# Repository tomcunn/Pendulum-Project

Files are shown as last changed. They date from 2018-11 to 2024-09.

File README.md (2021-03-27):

# Pendulum-Project
Inverted Pendulum code runs a stepper motor to control the position of a cart equipped with a pendulum. 

# Issues
* One of the key things to overcome was how to implement the encoder. One of the problems was drift of the encoder when I tried to implement the code myself. I ended up using an encoder library which solved the issue because they were using X4 encoding. This means that the position is updated on every edge of both channels. The overall accuracy of the cheap encoders is pretty incredible. 

* Another issue is the speed of the stepper, overall steppers are pretty slow and acceleration limited. Translating the code from timing pulses, to steps, to inches, to speeds is a little cumbersome in the code. Overall the cheap stepper drivers have worked just fine.

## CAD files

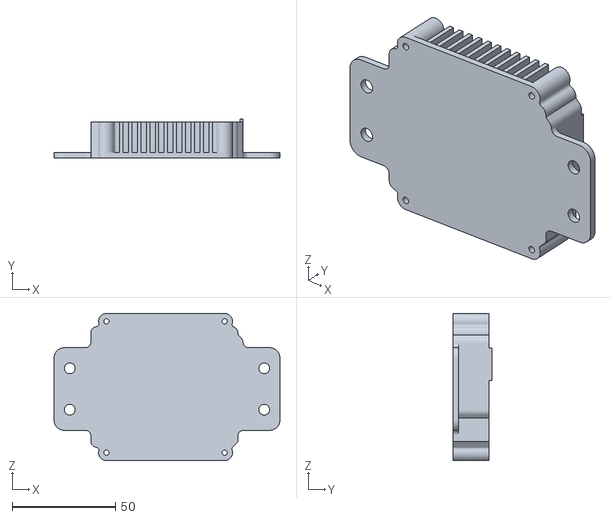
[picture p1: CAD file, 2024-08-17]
MechanicalDesignFiles/stl/Pendulum_Arduino_Case.stl
109.2 x 18.7 x 71.1

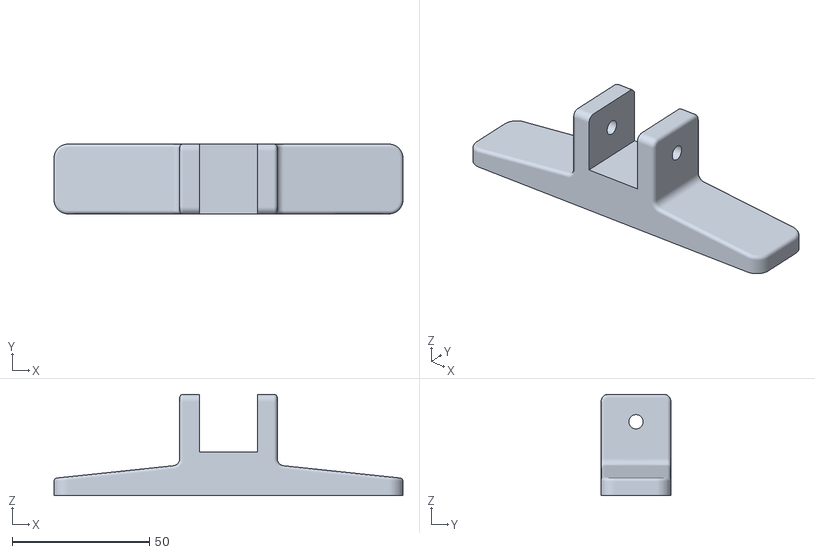
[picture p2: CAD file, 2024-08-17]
MechanicalDesignFiles/stl/Foot.stl
127.0 x 25.4 x 36.9

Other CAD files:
MechanicalDesignFiles/fusion_files/ArduinoUnoCasePendulum.f3d

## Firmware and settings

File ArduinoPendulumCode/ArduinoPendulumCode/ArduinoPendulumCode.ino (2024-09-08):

//**************************************
//*   Open Pendulum Control Platform Interface
//*   8/25/2024
//*   Cunningham
//***************************************

#include <avr/io.h>
#include <avr/interrupt.h>
#define ENCODER_OPTIMIZE_INTERRUPTS
#include <Encoder.h>


//Hardware Assignments
#define  LIMIT_HOME   A3
#define LED_GREEN  10  
#define LED_YELLOW 9
#define LED_RED 8
#define  DIR 11
#define  STEP 12
#define  SWITCH1 4
#define  SWITCH2 A2
#define  EncoderChannel_A  2
#define  EncoderChannel_B  3

#define  MAX_CART_VELOCITY  500  //875
#define  MAX_CART_ACCELERATION  50 //100

//Function prototypes
void  SetupTimer1(void);
void  SetupTimer0(void);

//Global Variables
uint8_t RunTask_10ms = 0;


volatile unsigned int StepSpeed = 0;

//Create and instance of the encoder module
Encoder PendulumPosition(EncoderChannel_A, EncoderChannel_B);

  //Create a structure for movement data
struct MovementParms
{
  signed int Count;
  signed int Position;
  signed int Velocity;
  signed int Acceleration;
  signed int Direction;
};

struct PendulumData
{
  //Create instance of three structures 
  volatile struct MovementParms DesiredCart;
  volatile struct MovementParms CurrentCart;
  volatile struct MovementParms EncoderValue;
};

PendulumData pd;

//**************************************
//  Interrupt used to generate the servo 
//  pulses
//  The lower the address the higher is the priority level
//  Vector Address 12 
//**************************************
ISR(TIMER1_COMPA_vect)  
{   
   if(StepSpeed < 64000)
   {
     //Check the direction pin and determine the position
     if(pd.CurrentCart.Direction == 1)
     {
        digitalWrite(DIR,1);
        pd.CurrentCart.Count++;
     }
     else
     {
       digitalWrite(DIR,0);
       pd.CurrentCart.Count--;
     }
  
     //Step once
     digitalWrite(STEP,1);
     digitalWrite(STEP,0);
   }
   //Interrupt occurs when timer matches this value
   //Larger velocity means smaller OCR1A value
   //StepSpeed is calculated using another function and then stored 
   //in a global variable to be accessed by the interrupt routine
   OCR1A = StepSpeed;
}

//**************************************
//  10 ms Task Rate
//  Creates a periodic Task 
//  Vector Address 15
//**************************************
ISR(TIMER0_COMPA_vect)
{
  RunTask_10ms = 1;
}

//*******************************************
// WriteStepSize
//
// Pass in a velocity and update the step size
// global variable which is read by the interrupt
// to generate the stepper pulses. Speed is in 
// the units mm/sec. 
//*******************************************
void WriteStepSize(signed int Speed)
{
  //Set the direction pin based on the sign of the speed
  if(Speed > 0)
  {
     pd.CurrentCart.Direction = 1;
  }
  else
  {
     pd.CurrentCart.Direction = 0;
  } 
  
  //Check to prevent overflows, StepSpeed is 16 bit
  if(Speed > 2 || Speed < -2)
  {
     //This is derived from the table above using a Power trendline
     StepSpeed = (signed int)(591733/(abs(Speed)));
  }
  //This is like setting it to zero speed
  else
  {
     StepSpeed = 65000;
  }
}

//***********************************
//  MotionAccelerationControl
//
//
//***********************************
void MotionAccelerationControl(void)
{
   //Acceleration is a signed value
   //If positive check to make sure it is not bigger than max V
   //else check the - max speed
   
   if(pd.DesiredCart.Acceleration >= 0)
   {
      if(pd.CurrentCart.Velocity < (MAX_CART_VELOCITY + pd.DesiredCart.Acceleration))
      {
         pd.CurrentCart.Velocity += pd.DesiredCart.Acceleration; 
      }
      else
      {
        pd.CurrentCart.Velocity = MAX_CART_VELOCITY;
      }
   }
   else
   {
      if(pd.CurrentCart.Velocity > (-MAX_CART_VELOCITY + pd.DesiredCart.Acceleration))
      {
         pd.CurrentCart.Velocity += pd.DesiredCart.Acceleration;
      }
      else
      {
         pd.CurrentCart.Velocity = -MAX_CART_VELOCITY;
      }
   }

   WriteStepSize(pd.CurrentCart.Velocity);
}
//*********************************************
//  SetupTimer0
//
//  Used to generate the 10 ms task rate
//*********************************************
void SetupTimer0()
{
  TCCR0A = 0; // set entire TCCR0A register to 0
  TCCR0B = 0; // same for TCCR0B
  TCNT0  = 0; //initialize counter value to 0
  // set compare match register for 2khz increments
  OCR0A = 155;// = (16*10^6) / (100*1024) - 1 = 155(must be <256)
  // turn on CTC mode
  TCCR0A |= (1 << WGM01);
  // 1024 prescaler - page 142 of datasheet
  TCCR0B |= (1 << CS00); 
  TCCR0B |= (1 << CS02);  
  // enable timer compare interrupt
  TIMSK0 |= (1 << OCIE0A);
}

//*********************************************
// SetupTimer1
//
//  Used to generate the stepper motor pulses
//********************************************
void SetupTimer1()
{
  //TCCRnA/B- Stands for Timer/Counter Control Registers.
  TCCR1A = 0;
  TCCR1B = 0;

  //TCNTn- Stands for Timer/Counter Register.
  TCNT1 = 0; // initialize the counter from 0

  //OCRnA/B- Stands for Output Compare Register.
  OCR1A = 65000; // sets the counter compare value

  //TIMSKn- Stands for Timer/Counter Mask In Registers.
  TCCR1B |= (1<<WGM12); // enable the CTC mode
  TCCR1B |= (1<<CS11); // 1/8 Prescale, 0 prescale was not working

  TIMSK1 |= (1<<OCIE1A); 
}



//****************************************
//  Setup
//
//****************************************
void setup()
{
  //Initialize Variables
  pd.CurrentCart.Velocity = 0;
  pd.DesiredCart.Velocity = 0;
  pd.CurrentCart.Count = 0;
  pd.DesiredCart.Acceleration = 1;

  //Setup Inputs
  pinMode(LIMIT_HOME, INPUT);
  pinMode(SWITCH1, INPUT);
  pinMode(SWITCH2, INPUT);
  pinMode(EncoderChannel_A, INPUT);
  pinMode(EncoderChannel_B, INPUT);

  //Setup Outputs
  pinMode(LED_GREEN,OUTPUT);
  pinMode(LED_YELLOW,OUTPUT);
  pinMode(LED_RED,OUTPUT);
  pinMode(STEP,OUTPUT);
  pinMode(DIR,OUTPUT);

  //Disable interrupts
  cli();
  
  //Setup Timers
  SetupTimer0();

  SetupTimer1();
  
  //enable interrupts
  sei();
  Serial.begin(115200);
}

//*********************************************
// Return Home
//
//********************************************
bool ReturnHome()
{
   bool home = false;

   digitalWrite(LED_RED,HIGH);
   digitalWrite(LED_GREEN,HIGH);
   
   if(pd.CurrentCart.Position > 5)
   {
      pd.DesiredCart.Velocity = -100;
   }
   else if(pd.CurrentCart.Position < -5)
   {
     pd.DesiredCart.Velocity = 100;
   }
   
   //Determine which direction to go
   if(!digitalRead(LIMIT_HOME))
   {
      pd.CurrentCart.Count = 0;
      pd.DesiredCart.Velocity = 0;
      pd.CurrentCart.Velocity = 0;
      pd.DesiredCart.Acceleration = 0;
      home = true;
   }
   WriteStepSize(pd.DesiredCart.Velocity);
   return home;
}

void PID_Loop()
{
  int error = 0;
  static int pre_error = 0;

  error = pd.EncoderValue.Count;

  //Try
  // P = 0.75
  // D = 2.0

  // P = 0.6
  // D = 4.0  Better

  // P = 0.6
  // D = 8.0 
  pd.DesiredCart.Acceleration = (int)((float)error * 0.6f) + ((float)(error - pre_error) * 8.0f) ;
  pre_error = error;  
}

void SendSerialData()
{
   // Send the three structures as binary data
   Serial.write((byte*)&pd,  sizeof(pd));
}

void loop()
{
  static int counter;
  static int previous_position;
  static bool homed = false;
  static bool homing = false;
  static bool start_control = false;

  if(RunTask_10ms)
  {
    counter++;
    if(counter > 2)
    {
      //SendSerialData();
      counter = 0;
    }
    //The Encoder has 2400 pulses per rev
    pd.EncoderValue.Count = -1*PendulumPosition.read();
    pd.EncoderValue.Position = (signed int)((float)pd.EncoderValue.Count/6.66666);
    
    //Turn the number of counts in a position in mm
    pd.CurrentCart.Position = (signed int)((float)pd.CurrentCart.Count/3.3799);

    //Serial.println(pd.EncoderValue.Position);

    digitalWrite(LED_YELLOW,HIGH);
    
    if(digitalRead(SWITCH2))
    {
      start_control = true;
      digitalWrite(LED_GREEN,HIGH);
    }
    else if(digitalRead(SWITCH1))
    {
      start_control = false;
      digitalWrite(LED_RED,HIGH);
    }


    //If both Switches are pressed return home
    if(digitalRead(SWITCH2) && digitalRead(SWITCH1))
    {
      homing = true;
      start_control = false;
    }

    //Exit the homing logic.    
    if(homed == true)
    {
      homing = false;
      homed = false;
    }

    //Return back home using this function
    if((homing==true) && (homed == false))
    {
      start_control = false;
      homed = ReturnHome();
    }
    else
    {
       if(start_control == true)
       {
        PID_Loop();
        MotionAccelerationControl();
       }
       else
       {
        pd.CurrentCart.Velocity = 0;
        WriteStepSize(pd.CurrentCart.Velocity);
       }
    }

    if(pd.EncoderValue.Position > 10 || pd.EncoderValue.Position < -10)
    {
      start_control = false;
    }

    Serial.print(homing);
    Serial.print(",");
    Serial.print(homed);
    Serial.print(",");
    Serial.println(pd.CurrentCart.Position);


    pd.EncoderValue.Acceleration = TCNT0;
    pd.EncoderValue.Velocity = 75;
    pd.EncoderValue.Direction = 30000;
    RunTask_10ms = 0;
  }
}

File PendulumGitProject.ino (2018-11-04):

//**************************************
//*   AI Pendulum Control Platform Interface
//*   4/6/2018
//*   Cunningham
//***************************************

#include <avr/io.h>
#include <avr/interrupt.h>
#define ENCODER_OPTIMIZE_INTERRUPTS
#include <Encoder.h>

//Hardware Assignments
#define  EncoderChannel_A  2
#define  EncoderChannel_B  3
#define  Step 12
#define  Dir  11
#define  MAX_CART_VELOCITY  30000
#define  MAX_CART_ACCELERATION  2000

#define LED_GREEN  10  
#define LED_YELLOW 9
#define LED_RED 8

#define  PGAIN 750

//Function prototypes
void  SetupTimer1(void);
void  SetupTimer0(void);
void  Encoder_ISR(void);
void  WriteStepSize(int Speed);
void  MotionVelocityControl(void);
void  MotionAccelerationControl(void);

//Create a structure for movement data
struct MovementParms
{
  signed int Position;
  signed int Velocity;
  signed int Acceleration;
  bool Direction;
};

//Create instance of three structures 
volatile struct MovementParms DesiredCart;
volatile struct MovementParms CurrentCart;
volatile struct MovementParms EncoderValue;

//Static Variables that are accessed in interrupts
volatile unsigned int abs_Current_Velocity = 0;
volatile unsigned int Counter = 0;
volatile unsigned int StepSpeed = 0;
volatile signed long timestep = 0;
volatile bool RunTask_10ms = 0;
byte SerialControlData1 = 0;
byte SerialControlData2 = 0;
bool SerialControlDirection = 0;
static bool ReturnHomeFlag = 0;
static unsigned int EncoderStableCount = 0;

byte serial_buffer[5] = {0,0,0,0,0};
int ByteCount;
static int integrator = 0;
Encoder PendulumPosition(EncoderChannel_A, EncoderChannel_B);

//**************************************
//  Interrupt used to generate the servo 
//  pulses
//  The lower the address the higher is the priority level
//  Vector Address 12 
//**************************************
ISR(TIMER1_COMPA_vect)  
{   
   if(StepSpeed < 64000)
   {
     //Check the direction pin and determine the position
     if(CurrentCart.Direction == 1)
     {
        digitalWrite(Dir,1);
        CurrentCart.Position++;
     }
     else
     {
       digitalWrite(Dir,0);
       CurrentCart.Position--;
     }
  
     //Step once
     digitalWrite(Step,1);
     digitalWrite(Step,0);
   }
   //Interrupt occurs when timer matches this value
   //Larger velocity means smaller OCR1A value
   //StepSpeed is calculated using another function and then stored 
   //in a global variable to be accessed by the interrupt routine
   OCR1A = StepSpeed;
}

//**************************************
//  10 ms Task Rate
//  Creates a periodic Task 
//  Vector Address 15
//**************************************
ISR(TIMER0_COMPA_vect)
{
  //Check to see if the flag was not cleared, this will track 
  //overruns in the 10ms task
  if(RunTask_10ms)
  {
    digitalWrite(LED_BUILTIN,1);
  }
  RunTask_10ms = 1;
}

//*******************************************
// WriteStepSize
//
// Pass in a velocity and update the step size
// global variable which is read by the interrupt
// to generate the stepper pulses. Speed is in 
// the units mm/min. 
//*******************************************
void WriteStepSize(signed int Speed)
{
  //Set the direction pin based on the sign of the speed
  if(Speed > 0)
  {
     CurrentCart.Direction = 1;
  }
  else
  {
     CurrentCart.Direction = 0;
  } 
  // Conversion Factor
  //  20000 mm      1 min      360 deg     1 rev       step          4,444 step
  // ----------- x -------- x -------- x -------- x ------------ =  ---------
  //     min        60 sec      rev        120 mm     0.225 deg       sec
  //
  //   16,000,000 cycles      1 sec            3,600 cycles
  //   ----------------- x --------------- = -----------
  //       1 sec             4,444 step          
  //  16,000,000/4,444    = 3,600 clock cycles  (20000 mm/min)
  //  16,000,000/2,222    = 7,200 clock cycles  (10000 mm/min)
  //  16,000,000/666      = 24,024 clock cycles  (3000 mm/min)
  
  //For some reason the prescale set to zero causes problems, so 8 is the minimum
  //which means the clock is 16,000,000/8=2,000,000
  //  2,000,000/4,444   = 450 clock cycles  (20000 mm/min)
  //  2,000,000/2,222    = 900 clock cycles  (10000 mm/min)
  //  2,000,000/666      = 3003 clock cycles (3000 mm/min)

  //To compute position it is 
  // Conversion Factor
  //    360 deg     1 rev       step          13.33 steps
  //  -------- x -------- x ------------ =  ---------
  //     rev        120 mm     0.225 deg        mm

  
  
  //Check to prevent overflows, StepSpeed is 16 bit
  if(Speed > 700 || Speed < -700)
  {
     //This is derived from the table above using a Power trendline
     StepSpeed = (signed int)(9048739L/(abs(Speed)));
  }
  //This is like setting it to zero speed
  else
  {
     StepSpeed = 65000;
  }
}
//*******************************************
//  Configure Timer 1
//*******************************************

void SetupTimer1()
{
  //TCCRnA/B- Stands for Timer/Counter Control Registers.
  TCCR1A = 0;
  TCCR1B = 0;

  //TCNTn- Stands for Timer/Counter Register.
  TCNT1 = 0; // initialize the counter from 0

  //OCRnA/B- Stands for Output Compare Register.
  OCR1A = 65000; // sets the counter compare value

  //TIMSKn- Stands for Timer/Counter Mask In Registers.
  TCCR1B |= (1<<WGM12); // enable the CTC mode
  TCCR1B |= (1<<CS11); // 1/8 Prescale, 0 prescale was not working

  TIMSK1 |= (1<<OCIE1A); 
}

//*********************************************
//  Configure Timer 0
//*********************************************
void SetupTimer0()
{
  TCCR0A = 0; // set entire TCCR0A register to 0
  TCCR0B = 0; // same for TCCR0B
  TCNT0  = 0; //initialize counter value to 0
  // set compare match register for 2khz increments
  OCR0A = 155;// = (16*10^6) / (100*1024) - 1 = 155(must be <256)
  // turn on CTC mode
  TCCR0A |= (1 << WGM01);
  // 1024 prescaler - page 142 of datasheet
  TCCR0B |= (1 << CS00); 
  TCCR0B |= (1 << CS02);  
  // enable timer compare interrupt
  TIMSK0 |= (1 << OCIE0A);
}
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

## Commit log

2024-08-17 Adding in an .stl to see if the viewer is present in github.
    [Foot.stl]
2024-08-17 Added in arduino case.
    [Pendulum_Arduino_Case.stl]
2024-08-17 Adding in fusion files
    [ArduinoUnoCasePendulum.f3d]
2024-09-08 Fixed issue with scaling of the velocity, now everything tests correctly.
    [ArduinoPendulumCode.ino]
2024-09-08 Adding in a PID Loop, code needs some cleanup for homing. A statemachine would be nice.
